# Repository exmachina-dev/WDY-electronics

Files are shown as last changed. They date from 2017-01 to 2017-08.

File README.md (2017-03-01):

```
_ _ _ ___  _   _    ____ _    ____ ____ ___ ____ ____ _  _ _ ____ ____ 
| | | |  \  \_/  __ |___ |    |___ |     |  |__/ |  | |\ | | |    [__  
|_|_| |__/   |      |___ |___ |___ |___  |  |  \ |__| | \| | |___ ___] 
                                                                        
```

# WDY electronics

This repo contains all necessary files to design and produce PCBs for the WDY product range.

## File format and folder structure

Documentation files should be in PDF. Board image files can be in PNG or PDF.

PCB Design file are in EAGLE Standard edition (7.4) file format.

These are general rules to help maintain a consistent folder structure:

* All libraries are placed inside the shared libraries repository. It can be found
  on [Github](https://github.com/exmchina-dev/eagle-resources)

* One board for each project folder.  

* Mutiples revisions can be placed inside a subfolder. i.e. HMI_Board/Rev A1  

* BOMs, partlists, spreadsheet should placed inside a BOMs/ folder.  

* Documentations files are in eagle-resources/doc or in doc/ inside a project folder.

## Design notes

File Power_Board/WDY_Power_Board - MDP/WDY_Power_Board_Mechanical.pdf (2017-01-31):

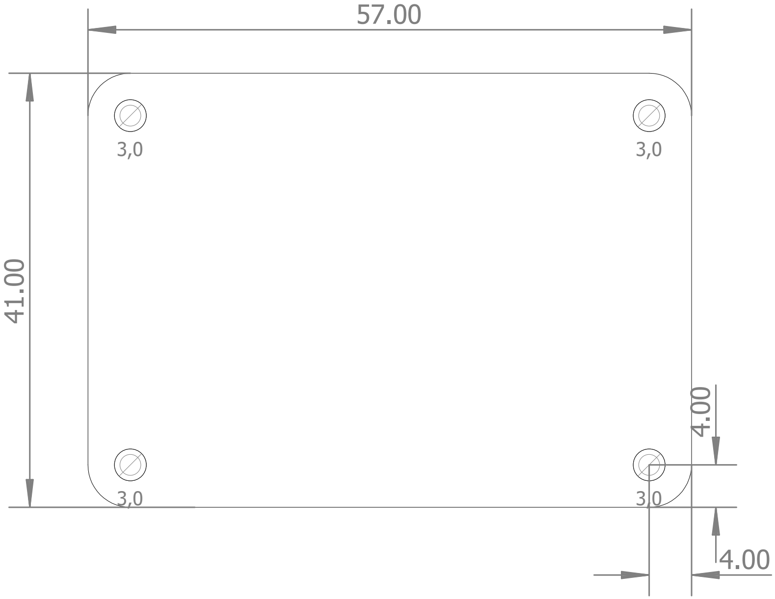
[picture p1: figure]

2017-01-25 11:11 AM f=3.04 C:\Users\Adrian\Documents\ExMachina\repos\WDY-electronics\Power_Board\WDY_Power_Board.brd

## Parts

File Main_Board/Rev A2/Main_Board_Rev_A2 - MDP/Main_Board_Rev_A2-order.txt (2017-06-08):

Quantity	Value	Package	Order code	Manufacturer	Manuf. Code	Availability	Price (from)	Description
1	4.7uF	CT3216	58R3271		F931A475MAA	1092	0.194	AVX (FORMERLY KNOWN AS NICHICON) - F931A475MAA - TANTALUM CAPACITOR, 4.7UF, 10V, 4 OHM, 0.2, 3216-12
10	100nF	C0603	06R4925		MC0603B104K250CT	4139	0.0040	MULTICOMP - MC0603B104K250CT - CERAMIC CAPACITOR, 0.1UF, 25V, X7R, 10%, 0603
3	10uF	CT3216	58R3260		F931A106MAA	1904	0.072	AVX (FORMERLY KNOWN AS NICHICON) - F931A106MAA - TANTALUM CAPACITOR, 10UF, 10V, 3 OHM, 0.2, 3216-12
1	4700pF	C0603	33R0458		MC0603B472K500CT	29799	0.013	MULTICOMP - MC0603B472K500CT - Multilayer Ceramic Capacitor, MC Series, 4700 pF,   10%, X7R, 50 V, 0603 [1608 Metric] 
26	0.1uF	C0603	06R4923		MC0603B104K160CT	46022	0.0040	MULTICOMP - MC0603B104K160CT - CERAMIC CAPACITOR, 0.1UF, 16V, X7R, 10%, 0603
2	18pF	C0603	06R5140		MC0603N180K500CT	3530	0.01	MULTICOMP - MC0603N180K500CT - CERAMIC CAPACITOR 18PF 50V, C0G, 10%, 0603
2	4.7uF	C0603	06X6198		MC0603X475K100CT	71030	0.027	MULTICOMP - MC0603X475K100CT - Multilayer Ceramic Capacitor, MC Series, 4.7  F,   10%, X5R, 10 V, 0603 [1608 Metric] 
4	2.2uF	C0603	01AC8938		GRT188R61H225KE13D	2465	0.113	MURATA - GRT188R61H225KE13D - CAP, MLCC, AEC-Q200, X5R, 2.2UF/50V, 0603
2	1000pF	C0603	06R4910		MC0603B102K500CT	4893	0.0040	MULTICOMP - MC0603B102K500CT - CERAMIC CAPACITOR 1000PF, 50V, X7R, 10%, 0603
2	22uF	C0805	33R0743		MC0805X226M6R3CT	108295	0.097	MULTICOMP - MC0805X226M6R3CT - Multilayer Ceramic Capacitor, MC Series, 22  F,   20%, X5R, 6.3 V, 0805 [2012 Metric] 
2	MBRS140	DO-214AA	83H7272	ON SEMICONDUCTOR	MBRS140T3G	794	0.153	ON SEMICONDUCTOR - MBRS140T3G - SCHOTTKY RECTIFIER, 1A, 40V, 403A
1	1812L110/24DR	LITTLEFUSE_SMD	22M2711		3557	44894	0.11	KEYSTONE - 3557 - FUSE CLIP, 0.8 X 2.8MM, PCB MOUNT
3	22-05-7028-02	7395-02	25M1728		22-05-7028	229	0.475	MOLEX - 22-05-7028 - WIRE-BOARD CONNECTOR HEADER 2 POSITION, 2.54MM
1	RB1-125BAG1A	WIZNET_RB1-125BAG1A	unknown					
1	5504F1-09S-02A-03	5504F1-09S-02A	18T0703		5504F1-09S-02A-03	682	0.836	MULTICOMP - 5504F1-09S-02A-03 - D SUB CONNECTOR, STANDARD, 9 POSITION, RECEPTACLE
4	22-05-7038-03	7395-03	26M6362		22-05-7038	40	0.52	MOLEX - 22-05-7038 - Wire-To-Board Connector, Right Angle, KK 7395 Series, Through Hole, Header, 3, 2.54 mm 
2	22-05-7058-05	7395-05	55H9619	MOLEX	22-05-7058	161	0.685	MOLEX - 22-05-7058 - WIRE-BOARD CONNECTOR HEADER 5 POSITION, 2.54MM
2	22-05-7048-04	7395-04	26M6363		22-05-7048	7713	0.601	MOLEX - 22-05-7048 - Wire-To-Board Connector, Right Angle, KK 7395 Series, Through Hole, Header, 4, 2.54 mm 
2	90814-0208	MOLEX_90814-0208	34R6216		90814-0208	279	0.667	MOLEX - 90814-0208 - Wire-To-Board Connector, Picoflex 90814 Series, Surface Mount, Header, 8, 1.27 mm 
1	90814-0206	MOLEX_90814-0206	34R6215		90814-0206	253	0.632	MOLEX - 90814-0206 - Wire-To-Board Connector, Picoflex 90814 Series, Surface Mount, Header, 6, 1.27 mm 
1	MSTBA2	MSTBA2	71C4161	FARNELL	1757242	2064	0.556	PHOENIX CONTACT - 1757242 - PIN HEADER, 2 POSITION, 5.08MM
1	22-27-2061-06	6410-06	56H0719	MOLEX	22-27-2061	115	0.276	MOLEX - 22-27-2061 - WIRE-BOARD CONNECTOR HEADER 6 POSITION, 2.54MM
1	USB3075-30-A	USB_MICROB_SMT	58T0863		USB3075-30-A	4042	0.418	GCT (GLOBAL CONNECTOR TECHNOLOGY) - USB3075-30-A - MICRO USB, 2.0 TYPE B, RECEPTACLE, SMT
1	1241050-5	2.54/2X5	98K5467		1241050-5	78	3.55	AMP - TE CONNECTIVITY - 1241050-5 - CONNECTOR, HEADER, 2.54MM, 10 POSITION
4	FIDUCIAL1X2	FIDUCIAL-1X2	unknown					
4	G6K-2G-Y	G6K-2G-Y	17C6944	OMRON COMPONENTS USA	G6K-2G-YDC24 BY OMR	0	3.25	OMRON ELECTRONIC COMPONENTS - G6K-2G-YDC24 BY OMR - SIGNAL RELAY, DPDT, 24VDC, 1A, SMD
1	0603PS-103KLB	0603	unknown					
1	15uH	WE-PD2_5848/5820	08P2818		744774115	0	1.27	WURTH ELEKTRONIK - 744774115 - INDUCTOR, UN-SHIELDED, 15UH, 1.9A, SMD
1	10uH	WE-PD2_5848/5820	08P2817		74477410	150	1.27	WURTH ELEKTRONIK - 74477410 - INDUCTOR, UN-SHIELDED, 10UH, 2.5A, SMD
9	Blue	CHIPLED_0603	15R2205		OVS-0603	115	0.159	MULTICOMP - OVS-0603 - LED, BLUE, 0.8MM X 1MM, 100MCD, 465NM
1	Red	CHIPLED_0603	15R2208		OVS-0608	3693	0.248	MULTICOMP - OVS-0608 - LED, RED, 0.8MM X 1MM, 300MCD, 625NM
4	MOUNT-PAD3,0	P3,0	unknown					
2	220	R0603	86T3577		MCMR06X2200FTL	400	0.0010	MULTICOMP - MCMR06X2200FTL - Surface Mount Thick Film Resistor, MCMR Series, 220 ohm, 0.1 W, -  1%, 75 V, 0603 [1608 Metric] 
4	49.9	R0603	86T3659		MCMR06X49R9FTL	15170	0.033	MULTICOMP - MCMR06X49R9FTL - Surface Mount Chip Resistor, Ceramic, MCMR Series, 49.9 ohm, 100 mW,   1%, 75 V, 0603 [1608 Metric] 
4	60.4	R0603	86T3680		MCMR06X60R4FTL	4840	0.027	MULTICOMP - MCMR06X60R4FTL - Surface Mount Chip Resistor, Ceramic, MCMR Series, 60.4 ohm, 100 mW,   1%, 75 V, 0603 [1608 Metric] 
11	4K7	R0603	86T3649		MCMR06X4701FTL	167711	0.033	MULTICOMP - MCMR06X4701FTL - Surface Mount Chip Resistor, Ceramic, MCMR Series, 4.7 kohm, 100 mW,   1%, 75 V, 0603 [1608 Metric] 
1	2K2	R0603	86T3578		MCMR06X2201FTL	9936	0.033	MULTICOMP - MCMR06X2201FTL - Surface Mount Chip Resistor, Ceramic, MCMR Series, 2.2 kohm, 100 mW,   1%, 75 V, 0603 [1608 Metric] 
9	10K	R0603	86T3506		MCMR06X1002FTL	93720	0.027	MULTICOMP - MCMR06X1002FTL - Surface Mount Thick Film Resistor, MCMR Series, 10 kohm, 0.1 W, -  1%, 75 V, 0603 [1608 Metric] 
4	0R	R0603	86T3500		MCMR06X000 PTL	14210	0.013	MULTICOMP - MCMR06X000 PTL - Surface Mount Chip Resistor, Ceramic, MCMR Series, 0 ohm, 100 mW,   0.05ohm, 75 V, 0603 [1608 Metric] 
10	1K5	R0603	86T3542		MCMR06X1501FTL	18540	0.033	MULTICOMP - MCMR06X1501FTL - Surface Mount Chip Resistor, Ceramic, MCMR Series, 1.5 kohm, 100 mW,   1%, 75 V, 0603 [1608 Metric] 
14	100	R0603	86T3504		MCMR06X1000FTL	65873	0.033	MULTICOMP - MCMR06X1000FTL - Surface Mount Chip Resistor, Ceramic, MCMR Series, 100 ohm, 100 mW,   1%, 75 V, 0603 [1608 Metric] 
2	374K	R0603	27W4235		CRCW0603374KFKEA.	3806	0.026	VISHAY - CRCW0603374KFKEA. - Surface Mount Thick Film Resistor, AEC-Q200 CRCW Series, 374 kohm, 100 mW, -  1%, 75 V 
11	1K	R0603	86T3505		MCMR06X1001FTL	60908	0.033	MULTICOMP - MCMR06X1001FTL - Surface Mount Thick Film Resistor, MCMR Series, 1 kohm, 0.1 W, -  1%, 75 V, 0603 [1608 Metric] 
3	2K7	R0603	86T3598		MCMR06X2701FTL	5441	0.033	MULTICOMP - MCMR06X2701FTL - Surface Mount Chip Resistor, Ceramic, MCMR Series, 2.7 kohm, 100 mW,   1%, 75 V, 0603 [1608 Metric] 
3	31K6	R0603	79M5962		MC0603SAF3162T5E	1508	0.0020	MULTICOMP - MC0603SAF3162T5E - RES, THICK FILM, 31K6, 1%, 0.1W, 0603
1	52K3	R0603	26M0962		MC0063W0603152K3	0		MULTICOMP - MC0063W0603152K3 - SMD Current Sense Resistors, MC Series, 52.3 kohm, 63 mW, -  1%, 50 V, 0603 [1608 Metric] 
2	33	R0603	86T3614		MCMR06X33R0FTL	0	0.033	MULTICOMP - MCMR06X33R0FTL - Surface Mount Thick Film Resistor, MCMR Series, 33 ohm, 100 mW, -  1%, 75 V, 0603 [1608 Metric] 
2	B3FS-1050	B3FS	18J2451	FARNELL	B3FS-1050	4815	2.02	OMRON ELECTRONIC COMPONENTS - B3FS-1050 - SWITCH, SPNO, EXTENDED
1	EXMACHINA-LOGO-NAME	EXM-LOGO-BASELINE	unknown					
1	MMBT2222AL	SOT-23	10N9478		MMBT2222ALT3G	13673	0.017	ON SEMICONDUCTOR - MMBT2222ALT3G - BIPOLAR TRANSISTOR, NPN, 40V SOT-23
6	TPB1,27	B1,27	unknown					
1	DP83848JSQ/NOPB	SQA40B	96W2841		DP83848JSQ/NOPB	695	1.3	TEXAS INSTRUMENTS - DP83848JSQ/NOPB - Ethernet Controller, 100 Mbps, IEEE 802.3, IEEE 802.3u, 3 V, 3.6 V, WQFN, 40 
1	MCP2561-E/SN	SOIC127P600X175-8N	12X8698		MCP2561-E/SN	901	0.984	MICROCHIP - MCP2561-E/SN - CAN Bus, Transceiver, CAN, LIN, 1, 1, 4.5 V, 5.5 V, SOIC 
1	AT24C512C-SSHM-B	SOIC127P600X175-8N	68T4128		AT24C512C-SSHM-B	181	1.39	MICROCHIP - AT24C512C-SSHM-B - SERIAL EEPROM, 512KBIT, 1MHZ, SOIC-8
1	LPC1768FBD100	SOT407-1	15R1840		LPC1768FBD100	4173	7.65	NXP - LPC1768FBD100 - 32 BIT MICROCONTROLLER MCU ARM CORTEX 100MHZ LQFP-100
1	TLV313	SOT23-DBV	95Y0395		TLV313IDBVT	1311	0.547	TEXAS INSTRUMENTS - TLV313IDBVT - OP-AMP, 1MHZ, 0.5V/US, SOT-23-5
2	SN74LVC2G17DBVR	SOT95P280X145-6N	76C4207	TEXAS INSTRUMENTS	SN74LVC2G17DBVR	2837	0.201	TEXAS INSTRUMENTS - SN74LVC2G17DBVR - SCHMITT TRIGGER BUFFER, 2BIT, SOT-23-6
3	SN74LVC3G17DCTR	SOP65P400X130-8N	90H3713	TEXAS INSTRUMENTS	SN74LVC3G17DCTR	2807	0.324	TEXAS INSTRUMENTS - SN74LVC3G17DCTR - SCHMITT TRIGGER BUFFER, SSOP-8
1	TPL0401A	SC-70-DCK	82Y6761		ISL90727WIE627Z-T7A	0	1.28	INTERSIL - ISL90727WIE627Z-T7A - DIGITAL POT, 10K, 128, SINGLE, SC-70-6
2	LT3686HDDPBF	DFN300X300X80-11N	78R8986		LT3686HDD#PBF	0	5.16	LINEAR TECHNOLOGY - LT3686HDD#PBF - PWM STEP-DOWN DC/DC CONVERTER, DFN10
1	ASE_50	ASE	84R2105		ASE-50.000MHZ-LC-T	1263	1.6	ABRACON - ASE-50.000MHZ-LC-T - OSCILLATOR, 50MHZ, 3.2 X 2.5MM, CMOS
1	FC-135	FC-135	31M4970		Q13FC13500004	291	0.762	EPSON - Q13FC13500004 - CRYSTAL, 32.768KHZ, 12.5PF, 3.2 X 1.5MM
1	ASE-12	ASE	40Y2118		ASE-12.000MHZ-LC-T	746	2.22	ABRACON - ASE-12.000MHZ-LC-T - OSC, 12MHZ, 3.2 X 2.5MM, LVCMOS
1	3000	3000	66F5622	KEYSTONE ELECTR	3000	13295	0.196	KEYSTONE - 3000 - RETAINER CONTACT, 12MM COIN CELL, SMD

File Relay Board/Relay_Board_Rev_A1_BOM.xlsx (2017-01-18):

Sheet: PdG
Project | WDY - Main Board
Board Name | Relay
Document | Bill of Materials
Author | AB
Date | 2017-01-18
Rev | A1

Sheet: BOM
Quantity | Value | Package | Order code | Manufacturer | Manuf. Code | Availability | Price (from) | Description
4 | 22-05-7028-02 | 2007041 | 25M1728 | Molex | 22-05-7028 | 201 | 0.475 | MOLEX - 22-05-7028 - WIRE-BOARD CONNECTOR HEADER 2 POSITION, 2.54MM
2 | 22-05-7038-03 | 2007069 | 26M6362 | Molex | 22-05-7038 | 40 | 0.133 | MOLEX - 22-05-7038 - Wire-To-Board Connector, Right Angle, KK 7395 Series, Through Hole, Header, 3, 2.54 mm
1 | 22-05-7048-04 | 2007100 | 26M6363 | Molex | 22-05-7048 | 1016 | 0.601 | MOLEX - 22-05-7048 - Wire-To-Board Connector, Right Angle, KK 7395 Series, Through Hole, Header, 4, 2.54 mm
6 | 0.1uF | C0603 | 06R4925 | MULTICOMP | MC0603B104K250CT | 4249 | 0.004 | MULTICOMP - MC0603B104K250CT - CERAMIC CAPACITOR, 0.1UF, 25V, X7R, 10%, 0603
4 | Blue | CHIPLED_0603 | 15R2205 | MULTICOMP | OVS-0603 | 0 | 0.188 | MULTICOMP - OVS-0603 - LED, BLUE, 0.8MM X 1MM, 100MCD, 465NM
4 | G6K-2G-Y | G6K-2G-Y | 82T9378 | OMRON Electronic | G6K-2G-Y 24DC | 338 | 3.83 | OMRON ELECTRONIC COMPONENTS - G6K-2G-Y 24DC - Signal Relay, G6K Series, Non Latching, DPDT, SMD, 1 A, 24 VDC
1 | MSTBA2 | MSTBA2 | 71C4161 | FARNELL | 1757242 | 828 | 0.667 | PHOENIX CONTACT - 1757242 - PIN HEADER, 2 POSITION, 5.08MM
8 | 100 | R0603 | 86T3504 | MULTICOMP | MCMR06X1000FTL | 92331 | 0.024 | MULTICOMP - MCMR06X1000FTL - Surface Mount Chip Resistor, Ceramic, MCMR Series, 100 ohm, 100 mW, 1%, 75 V, 0603 [1608 Metric]
4 | 4K7 | R0603 | 86T3649 | MULTICOMP | MCMR06X4701FTL | 202440 | 0.024 | MULTICOMP - MCMR06X4701FTL - Surface Mount Chip Resistor, Ceramic, MCMR Series, 4.7 kohm, 100 mW, 1%, 75 V, 0603 [1608 Metric]
4 | 1K5 | R0603 | 86T3542 | MULTICOMP | MCMR06X1501FTL | 8236 | 0.024 | MULTICOMP - MCMR06X1501FTL - Surface Mount Chip Resistor, Ceramic, MCMR Series, 1.5 kohm, 100 mW, 1%, 75 V, 0603 [1608 Metric]
4 | STPS3L40UF | SMB | 06X0873 | ST Microelectronics | STPS3L40UF | 6285 | 0.201 | STMICROELECTRONICS - STPS3L40UF - Rectifier Diode, Single, 40 V, 3 A, 500 mV, 75 A, 150 C
2 | SN74LVC2G17DBVR | SOT95P280X145-6N | 76C4207 | TEXAS INSTRUMENTS | SN74LVC2G17DBVR | 2988 | 0.159 | TEXAS INSTRUMENTS - SN74LVC2G17DBVR - SCHMITT TRIGGER BUFFER, 2BIT, SOT-23-6

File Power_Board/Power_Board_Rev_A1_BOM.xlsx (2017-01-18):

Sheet: PdG
Project | WDY - Main Board
Board Name | Main Board
Document | Bill Of Materials
Author | AB
Date | 2017-01-18
Rev | A1

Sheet: BOM
Quantity | Value | Package | Order code | Manufacturer | Manuf. Code | Availability | Price (from) | Description
4 | 2.2uF | C0603 | 01AC8938 | Murata | GRT188R61H225KE13D | 5810 | 0.097 | MURATA - GRT188R61H225KE13D - CAP, MLCC, AECQ200, X5R, 2.2UF/50V, 0603
2 | 1000pF | C0603 | 06R4910 | Multicomp | MC0603B102K500CT | 7447 | 0.004 | MULTICOMP - MC0603B102K500CT - CERAMIC CAPACITOR 1000PF, 50V, X7R, 10%, 0603
2 | 22uF | C0805 | 23T7233 | Multicomp | MC0805X226M6R3CT | 1149 | 0.051 | MULTICOMP - MCMT21N220F250CT - Multilayer Ceramic Capacitor, MLCC Series, 22 uF, 20%, XR, 6.8 V, 0805 [2012 Metric]
1 | STPS3L40UF | SMB | 06X0873 | ST Microelectronics | STPS3L40UF | 6563 | 0.214 | STMICROELECTRONICS - STPS3L40UF - Rectifier Diode, Single, 40 V, 3 A, 500 mV, 75 A, 150 C
2 | MBRS140 | DO-214AA | 83H7272 | ON SEMICONDUCTOR | MBRS140T3G | 684 | 0.166 | ON SEMICONDUCTOR - MBRS140T3G - SCHOTTKY RECTIFIER, 1A, 40V, 403A
1 | FUSE3557L | 3557-LITTLE | 22M2711 | Keystone | 3557 | 22952 | 0.112 | KEYSTONE - 3557 - FUSE CLIP, 0.8 X 2.8MM, PCB MOUNT
2 | 22-05-7028-02 | 2007041 | 25M1728 | Molex | 22-05-7028 | 283 | 0.475 | MOLEX - 22-05-7028 - WIRE-BOARD CONNECTOR HEADER 2 POSITION, 2.54MM
1 | 10uH | WE-PD2_5848/5820 | 08P2817 | Wurth Elektronik | 74477410 | 103 | 1.32 | WURTH ELEKTRONIK - 74477410 - INDUCTOR, UN-SHIELDED, 10UH, 2.5A, SMD
1 | 15uH | WE-PD2_5848/5820 | 08P2818 | Wurth Elektronik | 744774115 | 24 | 1.32 | WURTH ELEKTRONIK - 744774115 - INDUCTOR, UN-SHIELDED, 15UH, 1.9A, SMD
2 | Blue | CHIPLED_0603 | 15R2205 | Multicomp | OVS-0603 | 0 | 0.189 | MULTICOMP - OVS-0603 - LED, BLUE, 0.8MM X 1MM, 100MCD, 465NM
2 | Blue | CHIP-LED0603 | 15R2206 | Multicomp | OVS-0604 | 0 | 0.209 | MULTICOMP - OVS-0604 - LED, GREEN, 0.8MM X 1MM, 300MCD, 520NM
3 | 31k6 | R0603 | 58K4488 | Multicomp | MCMR06X3162FTL | 20297 | 0.012 | MULTICOMP - MC0063W060311K5 - RES, THICK FILM, 1K5, 1%, 0.063W, 0603
2 | 4k7 | R0603 | 86T3649 | Multicomp | MCMR06X4701FTL | 203820 | 0.027 | MULTICOMP - MCMR06X4701FTL - Surface Mount Chip Resistor, Ceramic, MCMR Series, 4.7 kohm, 100 mW, 1%, 75 V, 0603 [1608 Metric]
1 | 52k3 | R0603 | 26M0962 | Multicomp | MC0063W0603152K3 | 4499 | 0.024 | MULTICOMP - MC0063W0603152K3 - SMD Current Sense Resistors, MC Series, 52.3 kohm, 63 mW, - 1%, 50 V, 0603 [1608 Metric]
2 | 10k | R0603 | 86T3506 | Multicomp | MCMR06X1002FTL | 27199 | 0.027 | MULTICOMP - MCMR06X1002FTL - Surface Mount Thick Film Resistor, MCMR Series, 10 kohm, 0.1 W, - 1%, 75 V, 0603 [1608 Metric]
4 | 1k5 | R0603 | 58K4488 | Multicomp | MC0063W060311K5 | 20297 | 0.012 | MULTICOMP - MC0063W060311K5 - RES, THICK FILM, 1K5, 1%, 0.063W, 0603
2 | LT3686HDDPBF | DFN300X300X80-11N | 78R8986 | Linear Technology | LT3686HDD#PBF | 88 | 5.16 | LINEAR TECHNOLOGY - LT3686HDD#PBF - PWM STEP-DOWN DC/DC CONVERTER, DFN10
1 | MSTBA2 | MSTBA2 | 71C4161 | Phoenix Contact | 1757242 | 1130 | 0.667 | PHOENIX CONTACT - 1757242 - PIN HEADER, 2 POSITION, 5.08MM

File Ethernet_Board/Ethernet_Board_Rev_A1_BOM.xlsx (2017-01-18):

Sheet: PdG
Project | WDY - Main Board
Board Name | Ethernet Board
Document | Bill of Materials
Author | AB
Date | 2017-01-18
Rev | A1

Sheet: BOM
Quantity | Value | Package | Order code | Manufacturer | Manuf. Code | Availability | Price (from) | Description
1 | 4.7uF | CT3216 | 58R3271 | AVX | F931A475MAA | 1152 | 0.105 | AVX (FORMERLY KNOWN AS NICHICON) - F931A475MAA - TANTALUM CAPACITOR, 4.7UF, 10V, 4 OHM, 0.2, 3216-12
9 | 100nF | C0603 | 06R4925 | Multicomp | MC0603B104K250CT | 4249 | 0.014 | MULTICOMP - MC0603B104K250CT - CERAMIC CAPACITOR, 0.1UF, 25V, X7R, 10%, 0603
2 | 10uF | CT3216 | 58R3260 | AVX | F931A106MAA | 2581 | 0.063 | AVX (FORMERLY KNOWN AS NICHICON) - F931A106MAA - TANTALUM CAPACITOR, 10UF, 10V, 3 OHM, 0.2, 3216-12
1 | STPS3L40UF | SMB | 06X0873 | ST Microelectronics | STPS3L40UF | 6563 | 0.201 | STMICROELECTRONICS - STPS3L40UF - Rectifier Diode, Single, 40 V, 3 A, 500 mV, 75 A, 150 C
1 | 22-05-7028-02 | 2007041 | 25M1728 | Molex | 22-05-7028 | 283 | 0.475 | MOLEX - 22-05-7028 - WIRE-BOARD CONNECTOR HEADER 2 POSITION, 2.54MM
2 | 22-05-7068-06 | 2007161 | 25M1733 | Molex | 22-05-7068 | 11581 | 1.8 | MOLEX - 22-05-7068 - WIRE-BOARD CONNECTOR HEADER 6 POSITION, 2.54MM
1 | RB1-125BAG1A | WIZNET_RB1-125BAG1A | unknown | WIZnet | RB1-125BAG1A |  | 2.74 | Modular Connectors / Ethernet Connectors RJ-45 w/ Transformer connector/ude
2 | 220 | R0603 | 86T3577 | Multicomp | MCMR06X2200FTL | 400 | 0.024 | MULTICOMP - MCMR06X2200FTL - Surface Mount Thick Film Resistor, MCMR Series, 220 ohm, 0.1 W, - 1%, 75 V, 0603 [1608 Metric]
4 | 49.9 | R0603 | 86T3659 | Multicomp | MCMR06X49R9FTL | 21210 | 0.024 | MULTICOMP - MCMR06X49R9FTL - Surface Mount Chip Resistor, Ceramic, MCMR Series, 49.9 ohm, 100 mW, 1%, 75 V, 0603 [1608 Metric]
1 | 4K7 | R0603 | 86T3649 | Multicomp | MCMR06X4701FTL | 202910 | 0.024 | MULTICOMP - MCMR06X4701FTL - Surface Mount Chip Resistor, Ceramic, MCMR Series, 4.7 kohm, 100 mW, 1%, 75 V, 0603 [1608 Metric]
1 | 2K2 | R0603 | 86T3578 | Multicomp | MCMR06X2201FTL | 32492 | 0.024 | MULTICOMP - MCMR06X2201FTL - Surface Mount Chip Resistor, Ceramic, MCMR Series, 2.2 kohm, 100 mW, 1%, 75 V, 0603 [1608 Metric]
1 | DP83848JSQ/NOPB | SQA40B | 96W2841 | Texas Instrument | DP83848JSQ/NOPB | 492 | 1.32 | TEXAS INSTRUMENTS - DP83848JSQ/NOPB - Ethernet Controller, 100 Mbps, IEEE 802.3, IEEE 802.3u, 3 V, 3.6 V, WQFN, 40
1 | ASE_50 | ASE | 84R2105 | Abracon | ASE-50.000MHZ-LC-T | 3944 | 1.82 | ABRACON - ASE-50.000MHZ-LC-T - OSCILLATOR, 50MHZ, 3.2 X 2.5MM, CMOS

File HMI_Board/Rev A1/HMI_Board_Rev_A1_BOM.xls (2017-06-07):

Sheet: Sheet1
Project | WDY
Board Name | HMI Board
Author | AB
Date | 2017-06-06
Rev | A1

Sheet: BOM_HMI_Board
Qty | Value | Device | Package | Parts | Description | MPN | SKU | DataSheet | MOQ | QTY to order | Farnell
4 | Blue | OVS0603 | SML0603 | LED1, LED2, LED3, LED4 | LED | OVS0603 | 1716770 | http://datasheet.octopart.com/OVS-0603-Multicomp-datasheet-12472386.pdf | 10 | 10 | 0.245
4 | 1k | R-EU_R0603 | R0603 | R1, R2, R3, R4 | RESISTOR, European symbol | MCMR06X1001FTL | 2073348 | http://datasheet.octopart.com/MCMR06X1001FTL-Multicomp-datasheet-15896276.pdf | 10 | 10 | 0.0099
6 | 4k7 | R-EU_R0603 | R0603 | R5, R6, R7, R8, R9, R10 | RESISTOR, European symbol | MCMR06X4701FTL | 2073509 | http://datasheet.octopart.com/MCMR06X4701FTL-Multicomp-datasheet-15896276.pdf | 10 | 10 | 0.0099
1 | 90814-0206 | 90814-0206 | MOLEX_90814-0206 | U2 | CONN HEADER 06 POS 1.27MM SMD TIN | 90814-0206 | 1757024 | http://datasheet.octopart.com/908140206-Molex-datasheet-8333233.pdf | 10 | 10 | 0.68
1 | 90814-0208 | 90814-0208 | MOLEX_90814-0208 | U1 | CONN HEADER 8POS 1.27MM SMD TIN | 90814-0208 | 2426402 | http://datasheet.octopart.com/90814-0208-Molex-datasheet-13780264.pdf | 1 | 1 | 0.567
6 | B3FS-1015 | B3FS-1015 | B3FS | SW1, SW2, SW3, SW4, SW5, SW6 |  | B3FS-1015 | 1960996 | http://datasheet.octopart.com/B3FS1015-Omron-datasheet-10910168.pdf | 1 | 6 | 0.554
 |  |  |  |  |  |  |  |  |  |  | 2.0658
Version: 1.2.3.38126
Octopart Add-In is ready

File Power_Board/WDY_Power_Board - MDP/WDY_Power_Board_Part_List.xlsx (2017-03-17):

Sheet: PdG
Project | WDY - Main Board
Board Name | Power Board
Document | Part List
Author | AB
Date | 2017-02-10
Rev | A1

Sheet: BOM
Qty | Value | Parts | Description | MPN
4 | 2.2uF | C1, C2, C5, C6 | CAPACITOR, European symbol | GRT188R61H225KE13D
2 | 1000pF | C3, C4 | CAPACITOR, European symbol | MC0603B102K500CT
2 | 22uF | C7, C8 | CAPACITOR, European symbol | MCMT21N220F250CT
1 | STPS3L40UF | D1 | STMICROELECTRONICS | STPS3L40UF
2 | MBRS140 | D2, D3 | Redresseur Schottky, 40 V, 1 A, Une, DO-214AA, 2 Broche(s), 600 mV | MBRS140T3G
1 | FUSE3557L | F1 | Fuse | 3557
2 | 22-05-7028-02 | J1, J2 | CONNECTOR | 22-05-7028
1 | 10uH | L1 | SMD Power Inductor | 74477410
1 | 15uH | L2 | SMD Power Inductor | 744774115
2 | Blue | LED1, LED2 | LED | OVS-0603
2 | Blue | LED3, LED4 | LED | OVS-0604
3 | 31k6 | R1, R2, R7 | RESISTOR, European symbol | MCMR06X3162FTL
2 | 4k7 | R3, R4 | RESISTOR, European symbol | MCMR06X4701FTL
1 | 52k3 | R5 | RESISTOR, European symbol | MC0063W0603152K3
2 | 10k | R6, R8 | RESISTOR, European symbol | MCMR06X1002FTL
4 | 1k5 | R9, R10, R11, R12 | RESISTOR, European symbol | MC0063W060311K5
2 | LT3686HDDPBF | U1, U2 | 37V/1.2A Step-DownRegulator in 3mm × 3mm DFN | LT3686HDD#PBF
1 | MSTBA2 | X1 | PHOENIX | 1757242

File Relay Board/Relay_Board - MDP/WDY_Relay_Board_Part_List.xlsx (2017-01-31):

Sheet: PdG
Project | WDY - Main Board
Board Name | Relay Board
Document | Part List
Author | AB
Date | 2017-01-25
Rev | A1

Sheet: BOM
Qty | Value | Device | Package | Parts | Description | MPN
4 | 22-05-7028-02 | 22-05-7028-02 | 2007041 | J3, J4, J6, J7 | CONNECTOR | 22-05-7028
2 | 22-05-7038-03 | 22-05-7038-03 | 2007069 | J1, J2 | CONNECTOR | 22-05-7038
1 | 22-05-7048-04 | 22-05-7048-04 | 2007100 | J5 | CONNECTOR | 22-05-7048
6 | 0.1uF | C-EUC0603 | C0603 | C1, C2, C3, C4, C5, C6 | CAPACITOR, European symbol | MC0603B104K250CT
4 | Blue | LEDCHIPLED_0603 | CHIPLED_0603 | LED1, LED2, LED3, LED4 | LED | OVS-0603
4 | G6K-2G-Y | G6K-2G-Y | G6K-2G-Y | K1, K2, K3, K4 | Low Signal Relay | G6K-2G-Y 24DC
1 | MSTBA2 | MSTBA2 | MSTBA2 | X1 | PHOENIX | 1757242
8 | 100 | R-EU_R0603 | R0603 | R1, R2, R3, R4, R9, R10, R13, R16 | RESISTOR, European symbol | MCMR06X1000FTL
4 | 1K5 | R-EU_R0603 | R0603 | R11, R12, R14, R15 | RESISTOR, European symbol | MCMR06X1501FTL
4 | 4K7 | R-EU_R0603 | R0603 | R5, R6, R7, R8 | RESISTOR, European symbol | MCMR06X4701FTL
4 | STPS3L40UF | STPS3L40UF | SMB | D1, D2, D3, D4 | Zener Diode | STPS3L40UF
2 | SN74LVC2G17DBVR | SN74LVC2G17DBVR | SOT95P280X145-6N | U1, U2 | DUAL SCHMITT-TRIGGER BUFFER | SN74LVC2G17DBVR

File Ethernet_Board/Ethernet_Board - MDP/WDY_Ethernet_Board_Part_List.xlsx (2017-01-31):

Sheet: PdG
Project | WDY - Main Board
Board Name | Etheret Board
Document | Part List
Author | AB
Date | 2017-01-25
Rev | A1

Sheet: BOM
Qty | Value | Device | Package | Parts | Description | MPN
1 | 4.7uF | CPOL-EUCT3216 | CT3216 | C1 | POLARIZED CAPACITOR, European symbol | F931A475MAA
9 | 100nF | C-EUC0603 | C0603 | C2, C3, C5, C6, C7, C9, C10, C11, C12 | CAPACITOR, European symbol | MC0603B104K250CT
2 | 10uF | CPOL-EUCT3216 | CT3216 | C4, C8 | POLARIZED CAPACITOR, European symbol | F931A106MAA
1 | STPS3L40UF | STPS3L40UF | SMB | D1 | Diode Schottky 40V 3A Surface Mount SMBflat | STPS3L40UF
1 | 22-05-7028-02 | 22-05-7028-02 | 2007041 | J1 | CONNECTOR | 22-05-7028
2 | 22-05-7068-06 | 22-05-7068-06 | 2007161 | J2, J3 | CONNECTOR | 22-05-7068
1 | RB1-125BAG1A | RB1-125BAG1A | WIZNET_RB1-125BAG1A | P1 | Accessory RJ-45 With Transformer Connector - UDE | RB1-125BAG1A
2 | 220 | R-EU_R0603 | R0603 | R1, R2 | RESISTOR, European symbol | MCMR06X2200FTL
4 | 49.9 | R-EU_R0603 | R0603 | R3, R4, R5, R6 | RESISTOR, European symbol | MCMR06X49R9FTL
1 | 4K7 | R-EU_R0603 | R0603 | R7 | RESISTOR, European symbol | MCMR06X4701FTL
1 | 2K2 | R-EU_R0603 | R0603 | R8 | RESISTOR, European symbol | MCMR06X2201FTL
1 | DP83848JSQ/NOPB | DP83848JSQ/NOPB | SQA40B | U1 | Ethernet Phyter Single Port | DP83848JSQ/NOPB
1 | ASE_50 | ASE | ASE | X1 | 3.3Vdc CMOS SMD CRYSTAL CLOCK OSCILLATOR | ASE-50.000MHZ-LC-T

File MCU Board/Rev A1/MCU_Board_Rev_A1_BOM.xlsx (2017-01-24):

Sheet: PdG
Project | WDY - Main Board
Board Name | MCU Board
Document | Bill Of Materials
Author | AB
Date | 2017-01-24
Rev | A1

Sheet: BOM
Quantity | Value | Package | Order code | Manufacturer | Manuf. Code | Description
1 | 10uF | CT3216 | 58R3260 | AVX | F931A106MAA | AVX (FORMERLY KNOWN AS NICHICON) - F931A106MAA - TANTALUM CAPACITOR, 10UF, 10V, 3 OHM, 0.2, 3216-12
18 | 0.1uF | C0603 | 06R4923 | MULTICOMP | MC0603B104K160CT | MULTICOMP - MC0603B104K160CT - CERAMIC CAPACITOR, 0.1UF, 16V, X7R, 10%, 0603
2 | 18pF | C0603 | 06R5140 | MULTICOMP | MC0603N180K500CT | MULTICOMP - MC0603N180K500CT - CERAMIC CAPACITOR 18PF 50V, C0G, 10%, 0603
3 | 22-05-7068-06 | 2007161 | 25M1733 | MOLEX | 22-05-7068 | MOLEX - 22-05-7068 - WIRE-BOARD CONNECTOR HEADER 6 POSITION, 2.54MM
2 | 22-05-7028-02 | 2007041 | 25M1728 | MOLEX | 22-05-7028 | MOLEX - 22-05-7028 - WIRE-BOARD CONNECTOR HEADER 2 POSITION, 2.54MM
3 | 22-05-7038-03 | 2007069 | 26M6362 | MOLEX | 22-05-7038 | MOLEX - 22-05-7038 - Wire-To-Board Connector, Right Angle, KK 7395 Series, Through Hole, Header, 3, 2.54 mm
4 | 22-05-7048-04 | 2007100 | 26M6363 | MOLEX | 22-05-7048 | MOLEX - 22-05-7048 - Wire-To-Board Connector, Right Angle, KK 7395 Series, Through Hole, Header, 4, 2.54 mm
1 | 22-27-2061-06 | 1647397 | 56H0719 | MOLEX | 22-27-2061 | MOLEX - 22-27-2061 - WIRE-BOARD CONNECTOR HEADER 6 POSITION, 2.54MM
1 | USB3075-30-A | USB_MICROB_SMT | 58T0863 | GLOBAL CONNECTOR TECHNOLOGY | USB3075-30-A | GLOBAL CONNECTOR TECHNOLOGY - USB3075-30-A - MICRO USB, 2.0 TYPE B, RECEPTACLE, SMT
1 | 1241050-5 | 2.54/2X5 | 98K5467 | AMP | 1241050-5 | AMP - TE CONNECTIVITY - 1241050-5 - CONNECTOR, HEADER, 2.54MM, 10 POSITION
1 | 0603PS-103KLB | 603 | 2286330 | CoilCraft | 0603PS-103KLB | COILCRAFT 0603PS-103KLB Surface Mount Power Inductor, 0603PS Series, 10 µH, 380 mA, 210 mA, Shielded, 1.6 ohm
2 | Blue | CHIPLED_0603 | 15R2205 | MULTICOMP | OVS-0603 | MULTICOMP - OVS-0603 - LED, BLUE, 0.8MM X 1MM, 100MCD, 465NM
5 | 4K7 | R0603 | 86T3649 | MULTICOMP | MCMR06X4701FTL | MULTICOMP - MCMR06X4701FTL - Surface Mount Chip Resistor, Ceramic, MCMR Series, 4.7 kohm, 100 mW, 1%, 75 V, 0603 [1608 Metric]
4 | 0R | R0603 | 86T3500 | MULTICOMP | MCMR06X000 PTL | MULTICOMP - MCMR06X000 PTL - Surface Mount Chip Resistor, Ceramic, MCMR Series, 0 ohm, 100 mW, 0.05ohm, 75 V, 0603 [1608 Metric]
2 | 10K | R0603 | 86T3506 | MULTICOMP | MCMR06X1002FTL | MULTICOMP - MCMR06X1002FTL - Surface Mount Thick Film Resistor, MCMR Series, 10 kohm, 0.1 W, - 1%, 75 V, 0603 [1608 Metric]
3 | 1K5 | R0603 | 86T3542 | MULTICOMP | MCMR06X1501FTL | MULTICOMP - MCMR06X1501FTL - Surface Mount Chip Resistor, Ceramic, MCMR Series, 1.5 kohm, 100 mW, 1%, 75 V, 0603 [1608 Metric]
19 | 100 | R0603 | 86T3504 | MULTICOMP | MCMR06X1000FTL | MULTICOMP - MCMR06X1000FTL - Surface Mount Chip Resistor, Ceramic, MCMR Series, 100 ohm, 100 mW, 1%, 75 V, 0603 [1608 Metric]
3 | 33 | R0603 | 86T3614 | MULTICOMP | MCMR06X33R0FTL | MULTICOMP - MCMR06X33R0FTL - Surface Mount Thick Film Resistor, MCMR Series, 33 ohm, 100 mW, - 1%, 75 V, 0603 [1608 Metric]
6 | 1K | R0603 | 86T3505 | MULTICOMP | MCMR06X1001FTL | MULTICOMP - MCMR06X1001FTL - Surface Mount Thick Film Resistor, MCMR Series, 1 kohm, 0.1 W, - 1%, 75 V, 0603 [1608 Metric]
2 | B3FS-1015 | B3FS | 1960996 | OMRON ELECTRONICS | B3FS1015 | OMRON ELECTRONIC COMPONENTS B3FS1015 Tactile Switch, Non Illuminated, 24 V, 50 mA, 1.47 N, Solder
1 | MMBT2222AL | SOT-23 | 84K8795 | ON SEMICONDUCTOR | MMBT2222ALT1G | ON SEMICONDUCTOR - MMBT2222ALT1G - BIPOLAR TRANSISTOR, NPN, 40V,SOT-23
1 | AT24C512C-SSHM-B | SOIC127P600X175-8N | 68T4066 | MICROCHIP | AT24C02C-SSHM-B | MICROCHIP - AT24C02C-SSHM-B - SERIAL EEPROM, 2KBIT, 1MHZ, SOIC-8
1 | LPC1768FBD100 | SOT407-1 | 15R1840 | NXP | LPC1768FBD100 | NXP - LPC1768FBD100 - 32 BIT MICROCONTROLLER MCU ARM CORTEX 100MHZ LQFP-100
1 | TPL0401A | SC-70-DCK | 65T7357 | INTERSIL | ISL90728WIE627Z-TK | INTERSIL - ISL90728WIE627Z-TK - VOLATILE DIGITAL POTENTIOMETER
2 | SN74LVC3G17DCTR | SOP65P400X130-8N | 90H3713 | TEXAS INSTRUMENTS | SN74LVC3G17DCTR | TEXAS INSTRUMENTS - SN74LVC3G17DCTR - SCHMITT TRIGGER BUFFER, SSOP-8
1 | FC-135 | FC-135 | 31M4970 | EPSON | Q13FC13500004 | EPSON - Q13FC13500004 - CRYSTAL, 32.768KHZ, 12.5PF, 3.2 X 1.5MM
1 | ASE-12 | ASE | 40Y2118 | ABRACON | ASE-12.000MHZ-LC-T | ABRACON - ASE-12.000MHZ-LC-T - OSC, 12MHZ, 3.2 X 2.5MM, LVCMOS
1 | 3000 | 3000 | 66F5622 | KEYSTONE ELECTR | 3000 | KEYSTONE - 3000 - RETAINER CONTACT, 12MM COIN CELL, SMD

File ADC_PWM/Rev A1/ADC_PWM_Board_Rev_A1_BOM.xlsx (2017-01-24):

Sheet: PdG
Project | WDY - Main Board
Board Name | ADC/PWM Board
Document | Bill of Materials
Author | AB
Date | 2017-01-24
Rev | A1

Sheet: BOM
Quantity | Value | Package | Order code | Manufacturer | Manuf. Code | Availability | Price (from) | Description | Colonne1 | Colonne2 | Colonne3 | Colonne4 | Colonne5 | Colonne6 | Colonne7 | Colonne8 | Colonne9 | Colonne10
10 | 0.1uF | C0603 | 06R4925 | MULTICOMP | MC0603B104K250CT | 4249 | 0.004 | MULTICOMP - MC0603B104K250CT - CERAMIC CAPACITOR, 0.1UF, 25V, X7R, 10%, 0603
3 | 22-05-7028-02 | 2007041 | 25M1728 | MOLEX | 22-05-7028 | 195 | 0.475 | MOLEX - 22-05-7028 - WIRE-BOARD CONNECTOR HEADER 2 POSITION, 2.54MM
4 | 22-05-7048-04 | 2007100 | 26M6363 | MOLEX | 22-05-7048 | 11995 | 0.601 | MOLEX - 22-05-7048 - Wire-To-Board Connector, Right Angle, KK 7395 Series, Through Hole, Header, 4, 2.54 mm
3 | 22-05-7038-03 | 2007069 | 26M6362 | MOLEX | 22-05-7038 | 40 | 0.133 | MOLEX - 22-05-7038 - Wire-To-Board Connector, Right Angle, KK 7395 Series, Through Hole, Header, 3, 2.54 mm
1 | 22-05-7058-05 | 2007130 | 55H9619 | MOLEX | 22-05-7058 | 196 | 0.685 | MOLEX - 22-05-7058 - WIRE-BOARD CONNECTOR HEADER 5 POSITION, 2.54MM
1 | MSTBA2 | MSTBA2 | 71C4161 | FARNELL | 1757242 | 828 | 0.667 | PHOENIX CONTACT - 1757242 - PIN HEADER, 2 POSITION, 5.08MM
2 | 10K | R0603 | 86T3506 | MULTICOMP | MCMR06X1002FTL | 24613 | 0.024 | MULTICOMP - MCMR06X1002FTL - Surface Mount Thick Film Resistor, MCMR Series, 10 kohm, 0.1 W, - 1%, 75 V, 0603 [1608 Metric]
2 | 1K8 | R0603 | 86T3556 | MULTICOMP | MCMR06X1801FTL | 6621 | 0.024 | MULTICOMP - MCMR06X1801FTL - Surface Mount Chip Resistor, Ceramic, MCMR Series, 1.8 kohm, 100 mW, 1%, 75 V, 0603 [1608 Metric]
6 | 1K | R0603 | 86T3505 | MULTICOMP | MCMR06X1001FTL | 97318 | 0.024 | MULTICOMP - MCMR06X1001FTL - Surface Mount Thick Film Resistor, MCMR Series, 1 kohm, 0.1 W, - 1%, 75 V, 0603 [1608 Metric]
2 | 1K2 | R0603 | 86T3525 | MULTICOMP | MCMR06X1201FTL | 0 | 0.024 | MULTICOMP - MCMR06X1201FTL - Surface Mount Chip Resistor, Ceramic, MCMR Series, 1.2 kohm, 100 mW, 1%, 75 V, 0603 [1608 Metric]
5 | 100 | R0603 | 86T3504 | MULTICOMP | MCMR06X1000FTL | 92251 | 0.024 | MULTICOMP - MCMR06X1000FTL - Surface Mount Chip Resistor, Ceramic, MCMR Series, 100 ohm, 100 mW, 1%, 75 V, 0603 [1608 Metric]
3 | 2K7 | R0603 | 86T3649 | MULTICOMP | MCMR06X4701FTL | 202080 | 0.024 | MULTICOMP - MCMR06X4701FTL - Surface Mount Chip Resistor, Ceramic, MCMR Series, 4.7 kohm, 100 mW, 1%, 75 V, 0603 [1608 Metric]
1 | TLV313 | SOT23-DBV | 95Y0395 | TEXAS INSTRUMENTS | TLV313IDBVT | 1380 | 0.618 | TEXAS INSTRUMENTS - TLV313IDBVT - OP-AMP, 1MHZ, 0.5V/US, SOT-23-5
1 | HCPL0631 | SOIC08 | 52M7944 |  | HCPL-0631-500E | 505 | 3.28 | BROADCOM LIMITED - HCPL-0631-500E - OPTOCOUPLER, TRANSISTOR, 3750VRMS
1 | SN74LVC3G17DCTR | SOP65P400X130-8N | 90H3713 | TEXAS INSTRUMENTS | SN74LVC3G17DCTR | 1536 | 0.255 | TEXAS INSTRUMENTS - SN74LVC3G17DCTR - SCHMITT TRIGGER BUFFER, SSOP-8

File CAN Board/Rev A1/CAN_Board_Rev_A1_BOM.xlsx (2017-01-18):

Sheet: PdG
Project | WDY - Main Board
Board Name | CAN Board
Document | Bill Of Material
Author | AB
Date | 2017-01-18
Rev | A1

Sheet: BOM
Quantity | Value | Package | Order code | Manufacturer | Manuf. Code | Availability | Price (from) | Description
1 | 4700pF | C0603 | 33R0458 | Multicomp | MC0603B472K500CT | 74089 | 0.012 | MULTICOMP - MC0603B472K500CT - Multilayer Ceramic Capacitor, MC Series, 4700 pF, 10%, X7R, 50 V, 0603 [1608 Metric]
1 | 100nF | C0603 | 06R4925 | Multicomp | MC0603B104K250CT | 4249 | 0.014 | MULTICOMP - MC0603B104K250CT - CERAMIC CAPACITOR, 0.1UF, 25V, X7R, 10%, 0603
2 | 22-05-7028-02 | 22-05-7028 | 25M1728 | Molex | 22-05-7028 | 283 | 0.475 | MOLEX - 22-05-7028 - WIRE-BOARD CONNECTOR HEADER 2 POSITION, 2.54MM
1 | 5504F1-09S-02A-03 | 5504F1-09S-02A | 18T0703 | Multicomp | 5504F1-09S-02A-03 | 623 | 0.945 | MULTICOMP - 5504F1-09S-02A-03 - D SUB CONNECTOR, STANDARD, 9 POSITION, RECEPTACLE
2 | 60R4 | R0603 | 86T3680 | Multicomp | MCMR06X60R4FTL | 400 | 0.024 | MULTICOMP - MCMR06X60R4FTL - Surface Mount Chip Resistor, Ceramic, MCMR Series, 60.4 ohm, 100 mW, 1%, 75 V, 0603 [1608 Metric]
1 | MCP2561-E/SN | SOIC127P600X175-8N | 12X8698 | Microchip | MCP2561-E/SN | 1408 | 1.44 | MICROCHIP - MCP2561-E/SN - CAN Bus, Transceiver, CAN, LIN, 1, 1, 4.5 V, 5.5 V, SOIC
1 | MSTBA2 | MSTBA2 | 71C4161 | Phoenix Contact | 1757242 | 828 | 0.667 | PHOENIX CONTACT - 1757242 - PIN HEADER, 2 POSITION, 5.08MM

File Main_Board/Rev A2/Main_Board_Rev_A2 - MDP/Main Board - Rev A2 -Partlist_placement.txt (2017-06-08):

Partlist

Exported from Main_Board_Rev_A2.brd at 2017-06-08 11:09 AM

EAGLE Version 7.7.0 Copyright (c) 1988-2016 CadSoft

Assembly variant: 

Part     Value             Package             Library                        Position (mm)         Orientation

C1       4.7uF             CT3216              rcl                            (11 44)               MR90
C2       100nF             C0603               rcl                            (23.5 38)             R180
C3       100nF             C0603               rcl                            (23.5 50)             R180
C4       10uF              CT3216              rcl                            (36 44.5)             MR90
C5       4700pF            C0603               rcl                            (56 81.5)             R270
C6       100nF             C0603               rcl                            (28.2 39.9)           MR180
C7       100nF             C0603               rcl                            (36 39)               MR180
C8       100nF             C0603               rcl                            (28.2 45.1)           MR180
C9       10uF              CT3216              rcl                            (32 50)               MR270
C10      100nF             C0603               rcl                            (25.8 41.5)           MR0
C11      100nF             C0603               rcl                            (28.5 48)             MR180
C12      100nF             C0603               rcl                            (31 40)               MR90
C13      100nF             C0603               rcl                            (36.8 36.4)           R90
C14      100nF             C0603               rcl                            (48 79.5)             MR270
C15      10uF              CT3216              rcl                            (54.5 61)             MR0
C16      0.1uF             C0603               rcl                            (47.5 48.5)           MR90
C17      0.1uF             C0603               rcl                            (59.6 36)             R90
C18      0.1uF             C0603               rcl                            (49.5 25.6)           MR270
C19      18pF              C0603               rcl                            (48.4 35.7)           R270
C20      0.1uF             C0603               rcl                            (51 55)               MR180
C21      0.1uF             C0603               rcl                            (46.5 53.5)           MR0
C22      0.1uF             C0603               rcl                            (55 56.5)             MR90
C23      0.1uF             C0603               rcl                            (52.3 41)             MR180
C24      18pF              C0603               rcl                            (54.6 35.7)           R270
C25      0.1uF             C0603               rcl                            (58.5 48)             MR180
C26      0.1uF             C0603               rcl                            (58.5 53.5)           MR180
C27      0.1uF             C0603               rcl                            (47.5 13.6)           MR90
C28      0.1uF             C0603               rcl                            (71.5 20)             R180
C29      0.1uF             C0603               rcl                            (71.5 32.5)           R180
C30      0.1uF             C0603               rcl                            (71.5 41)             R180
C31      0.1uF             C0603               rcl                            (71.5 51.5)           R180
C32      0.1uF             C0603               rcl                            (71.2 46.5)           MR180
C33      0.1uF             C0603               rcl                            (71.4 26.4)           MR180
C34      0.1uF             C0603               rcl                            (56.5 14)             MR270
C35      4.7uF             C0603               rcl                            (14 11.5)             R180
C36      4.7uF             C0603               rcl                            (20.9 11.6)           R180
C37      0.1uF             C0603               rcl                            (17.2 70.1)           R0
C38      0.1uF             C0603               rcl                            (17.2 77.1)           R0
C39      0.1uF             C0603               rcl                            (17.2 72.3)           R0
C40      0.1uF             C0603               rcl                            (17.2 79.35)          R0
C41      0.1uF             C0603               rcl                            (17.2 74.85)          R0
C42      0.1uF             C0603               rcl                            (17.2 81.9)           R0
C43      0.1uF             C0603               rcl                            (24 87)               R270
C44      0.1uF             C0603               rcl                            (26.4 79.9)           R90
C45      0.1uF             C0603               rcl                            (20.1 70.2)           MR270
C46      2.2uF             C0603               rcl                            (80 82.5)             R180
C47      2.2uF             C0603               rcl                            (80 63)               R180
C48      1000pF            C0603               rcl                            (86.5 81)             R0
C49      1000pF            C0603               rcl                            (86.5 62)             R0
C50      2.2uF             C0603               rcl                            (78 96)               R180
C51      2.2uF             C0603               rcl                            (78 76)               R180
C52      22uF              C0805               rcl                            (77.6 85)             R0
C53      22uF              C0805               rcl                            (77.6 65.5)           R0
D1       MBRS140           DO-214AA            diode                          (78 92.5)             R0
D2       MBRS140           DO-214AA            diode                          (78 73)               R0
F1       1812L110/24DR     LITTLEFUSE_SMD      fuse2                          (93.5 73)             R270
J1       22-05-7028-02     7395-02             con-molex                      (5 58)                R270
J2       RB1-125BAG1A      WIZNET_RB1-125BAG1A con-wiznet                     (8.5 44)              R270
J3       5504F1-09S-02A-03 5504F1-09S-02A      con-multicomp                  (50 90.5)             R0
J4       22-05-7038-03     7395-03             con-molex                      (95 22.5)             R90
J5       22-05-7038-03     7395-03             con-molex                      (95 33)               R90
J6       22-05-7038-03     7395-03             con-molex                      (95 43.5)             R90
J7       22-05-7038-03     7395-03             con-molex                      (95 54)               R90
J8       22-05-7058-05     7395-05             con-molex                      (44.5 5)              R0
J9       22-05-7048-04     7395-04             con-molex                      (85 5)                R0
J10      22-05-7048-04     7395-04             con-molex                      (72.5 5)              R0
J11      22-05-7058-05     7395-05             con-molex                      (59.008 5)            R0
J12      22-05-7028-02     7395-02             con-molex                      (13.5 5)              R0
J13      22-05-7028-02     7395-02             con-molex                      (20.5 5)              R0
J14      90814-0208        MOLEX_90814-0208    Molex_By_element14_Batch_1     (19.4 93.9)           R0
J15      90814-0208        MOLEX_90814-0208    Molex_By_element14_Batch_1     (6.3 82)              R90
J16      90814-0206        MOLEX_90814-0206    Molex_By_element14_Batch_1     (6.3 67.7)            R90
J17      MSTBA2            MSTBA2              con-phoenix-508                (98 85.5)             R90
J18      22-27-2061-06     6410-06             con-molex                      (18 24)               R270
J19      USB3075-30-A      USB_MICROB_SMT      con-GlobalConnectorTechnology  (32.35 1.5)           R0
J20      1241050-5         2.54/2X5            con-amp                        (7 22)                R90
JP1      FIDUCIAL1X2       FIDUCIAL-1X2        SparkFun                       (3 8.5)               R0
JP2      FIDUCIAL1X2       FIDUCIAL-1X2        SparkFun                       (95.5 8)              R0
JP3      FIDUCIAL1X2       FIDUCIAL-1X2        SparkFun                       (6 92.5)              R0
JP4      FIDUCIAL1X2       FIDUCIAL-1X2        SparkFun                       (91 96)               R0
K1       G6K-2G-Y          G6K-2G-Y            relay                          (84 22.5)             R180
K2       G6K-2G-Y          G6K-2G-Y            relay                          (84 33)               R180
K3       G6K-2G-Y          G6K-2G-Y            relay                          (84 43.5)             R180
K4       G6K-2G-Y          G6K-2G-Y            relay                          (84 53.5)             R180
L1       0603PS-103KLB     0603                coilcraft                      (52.3 43)             MR0
L2       15uH              WE-PD2_5848/5820    Wurth-POWER_MAGNETICS-rev16f   (71.992 87)           R270
L3       10uH              WE-PD2_5848/5820    Wurth-POWER_MAGNETICS-rev16f   (71.992 67)           R270
LED1     Blue              CHIPLED_0603        led                            (46 73.1)             R180
LED2     Blue              CHIPLED_0603        led                            (77.5 20.5)           R180
LED3     Blue              CHIPLED_0603        led                            (77.5 31)             R180
LED4     Blue              CHIPLED_0603        led                            (77.5 41.5)           R180
LED5     Blue              CHIPLED_0603        led                            (77.5 52)             R180
LED6     Red               CHIPLED_0603        led                            (89 74.5)             R0
LED7     Blue              CHIPLED_0603        led                            (88 12)               R180
LED8     Blue              CHIPLED_0603        led                            (80.5 12)             R180
LED9     Blue              CHIPLED_0603        led                            (84.5 12)             R180
LED10    Blue              CHIPLED_0603        led                            (48.35 73.05)         R180
MP1      MOUNT-PAD3,0      P3,0                holes                          (4 96)                R0
MP2      MOUNT-PAD3,0      P3,0                holes                          (96 96)               R0
MP3      MOUNT-PAD3,0      P3,0                holes                          (4 4)                 R0
MP4      MOUNT-PAD3,0      P3,0                holes                          (96 4)                R0
R1       220               R0603               rcl                            (7.7 41.7)            MR180
R2       220               R0603               rcl                            (7.6 46.1)            MR180
R3       49.9              R0603               rcl                            (23.5 40)             R180
R4       49.9              R0603               rcl                            (23.5 43)             R180
R5       49.9              R0603               rcl                            (23.5 45)             R180
R6       49.9              R0603               rcl                            (23.5 48)             R180
R7       60.4              R0603               rcl                            (53.5 84.5)           R270
R8       60.4              R0603               rcl                            (50.5 84.5)           R90
R9       4K7               R0603               rcl                            (27.5 39)             R270
R10      2K2               R0603               rcl                            (38.5 40.6)           MR0
R11      10K               R0603               rcl                            (60.3 28.3)           R90
R12      4K7               R0603               rcl                            (56.2 30.7)           R0
R13      4K7               R0603               rcl                            (52.3 30.7)           R180
R14      0R                R0603               rcl                            (35.4 73.7)           R0
R15      0R                R0603               rcl                            (39 73.7)             R0
R16      10K               R0603               rcl                            (52 37)               MR270
R17      10K               R0603               rcl                            (60 73)               R270
R18      0R                R0603               rcl                            (63 72)               R180
R19      0R                R0603               rcl                            (63 74)               R180
R20      1K5               R0603               rcl                            (46 69.8)             R270
R21      100               R0603               rcl                            (91.1 22.5)           R180
R22      100               R0603               rcl                            (91.1 33)             R180
R23      100               R0603               rcl                            (91.1 43.5)           R180
R24      100               R0603               rcl                            (91.3 54)             R180
R25      60.4              R0603               rcl                            (46.8 9)              R90
R26      60.4              R0603               rcl                            (44.2 8.9)            R90
R27      374K              R0603               rcl                            (48.4 9)              R90
R28      4K7               R0603               rcl                            (75 22)               R0
R29      4K7               R0603               rcl                            (75 30.5)             R0
R30      374K              R0603               rcl                            (42.1 13.6)           R270
R31      4K7               R0603               rcl                            (75 43)               R0
R32      4K7               R0603               rcl                            (75 53.5)             R0
R33      100               R0603               rcl                            (75 20)               R180
R34      100               R0603               rcl                            (75 32.5)             R180
R35      1K5               R0603               rcl                            (77.5 24)             R90
R36      1K5               R0603               rcl                            (77.5 34.5)           R90
R37      100               R0603               rcl                            (75 41)               R180
R38      1K5               R0603               rcl                            (77.5 45)             R90
R39      1K5               R0603               rcl                            (77.5 55.5)           R90
R40      100               R0603               rcl                            (75 51.5)             R180
R41      1K                R0603               rcl                            (86.3 9)              R90
R42      1K                R0603               rcl                            (73.8 9)              R90
R43      2K7               R0603               rcl                            (57.108 9)            R270
R44      2K7               R0603               rcl                            (52.008 9)            R270
R45      2K7               R0603               rcl                            (63.508 9)            R270
R46      1K                R0603               rcl                            (59.008 9)            R90
R47      1K                R0603               rcl                            (53.908 9)            R90
R48      1K                R0603               rcl                            (61.508 9)            R90
R49      10K               R0603               rcl                            (12.2 8.8)            R270
R50      10K               R0603               rcl                            (19.2 8.8)            R90
R51      10K               R0603               rcl                            (14.8 8.8)            R270
R52      10K               R0603               rcl                            (21.8 8.8)            R90
R53      100               R0603               rcl                            (13.5 59)             R0
R54      100               R0603               rcl                            (13.5 64)             R0
R55      100               R0603               rcl                            (13.5 56.4)           R180
R56      100               R0603               rcl                            (13.5 61.5)           R180
R57      4K7               R0603               rcl                            (32 89.8)             R180
R58      4K7               R0603               rcl                            (28.5 89.85)          R0
R59      1K                R0603               rcl                            (13.5 70.1)           R0
R60      1K                R0603               rcl                            (13.5 72.3)           R0
R61      1K                R0603               rcl                            (13.5 74.85)          R0
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

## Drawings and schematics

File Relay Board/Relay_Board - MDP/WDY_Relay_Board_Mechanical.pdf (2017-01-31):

57.00

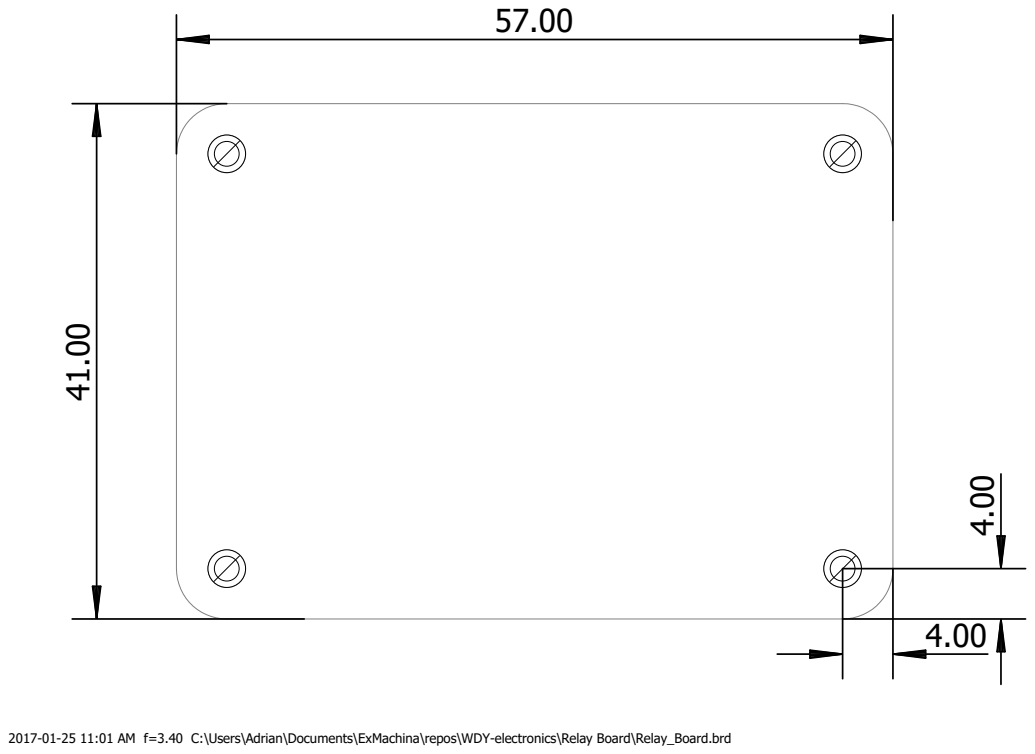
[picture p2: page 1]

2017-01-25 11:01 AM f=3.40 C:\Users\Adrian\Documents\ExMachina\repos\WDY-electronics\Relay Board\Relay_Board.brd 41.00

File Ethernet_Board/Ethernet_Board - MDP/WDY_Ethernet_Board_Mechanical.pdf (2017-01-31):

57.00 41.00

# 4.00 ⁴.00 ³,0

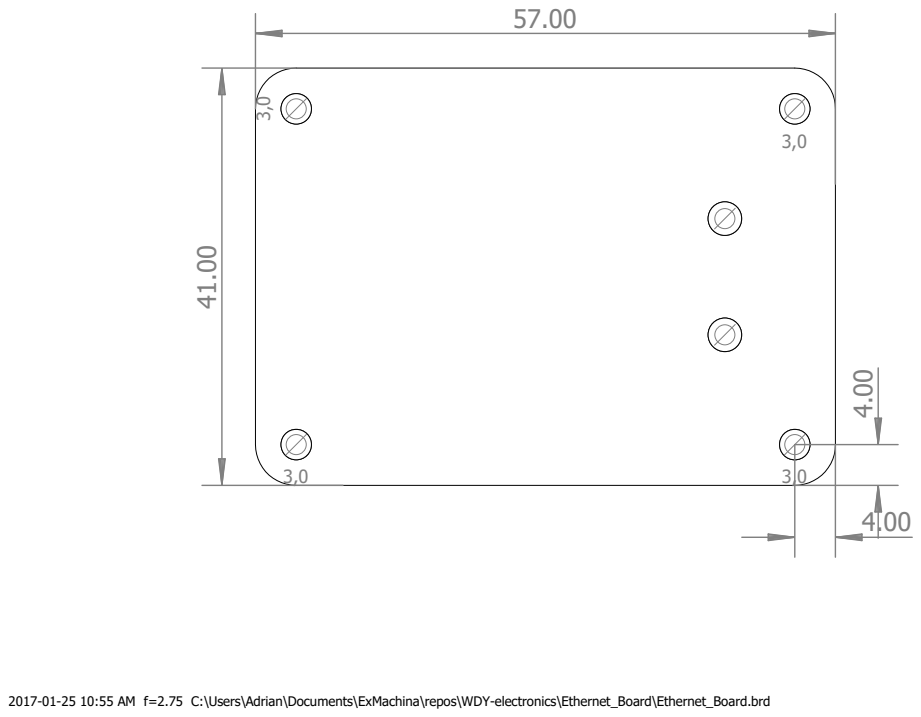
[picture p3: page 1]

2017-01-25 10:55 AM f=2.75 C:\Users\Adrian\Documents\ExMachina\repos\WDY-electronics\Ethernet_Board\Ethernet_Board.brd

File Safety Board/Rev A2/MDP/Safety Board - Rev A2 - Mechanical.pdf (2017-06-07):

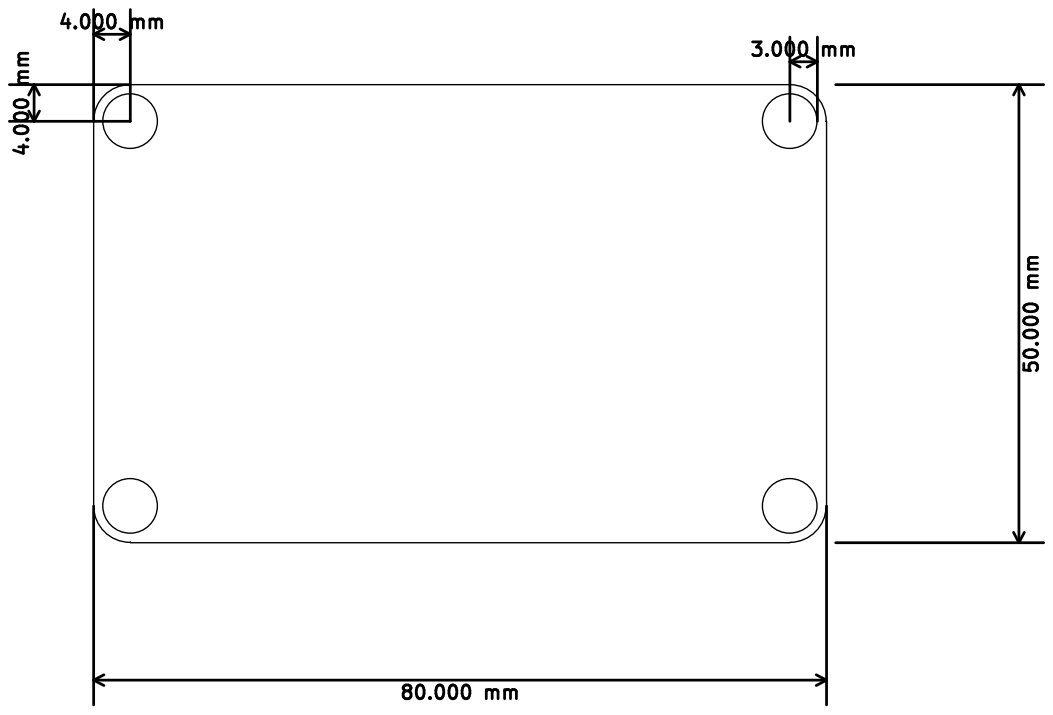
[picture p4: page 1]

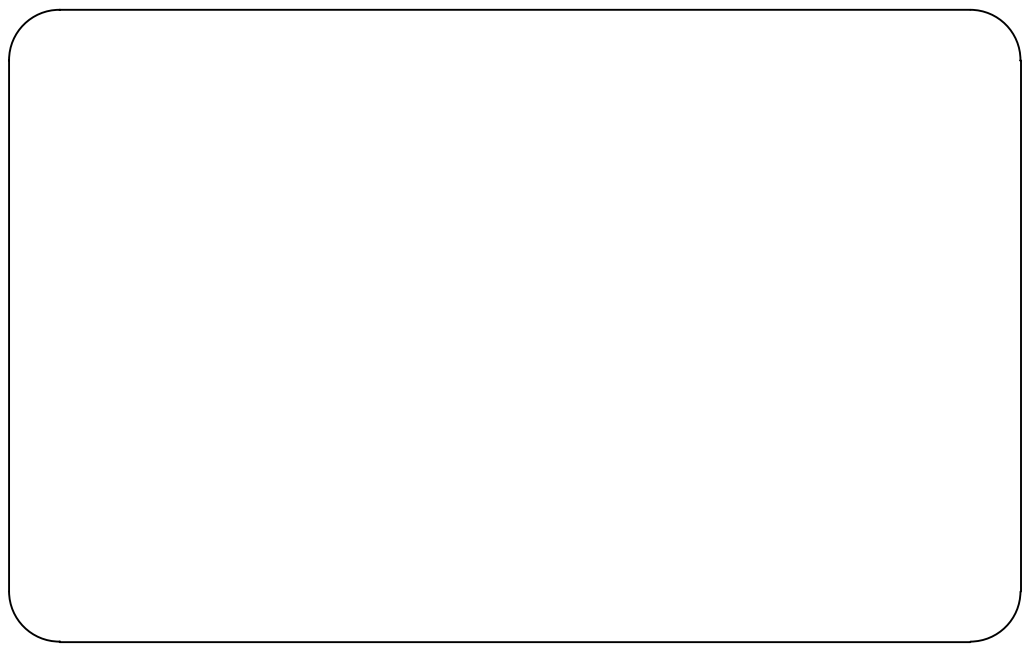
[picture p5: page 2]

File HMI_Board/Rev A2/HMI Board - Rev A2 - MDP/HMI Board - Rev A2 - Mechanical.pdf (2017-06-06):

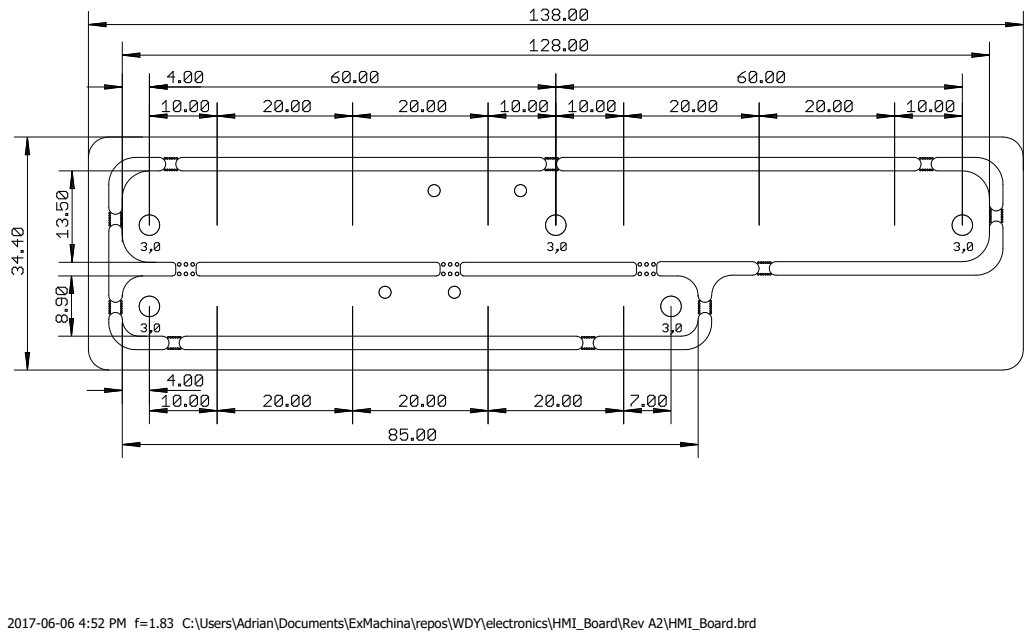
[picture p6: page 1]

2017-06-06 4:52 PM f=1.83 C:\Users\Adrian\Documents\ExMachina\repos\WDY\electronics\HMI_Board\Rev A2\HMI_Board.brd

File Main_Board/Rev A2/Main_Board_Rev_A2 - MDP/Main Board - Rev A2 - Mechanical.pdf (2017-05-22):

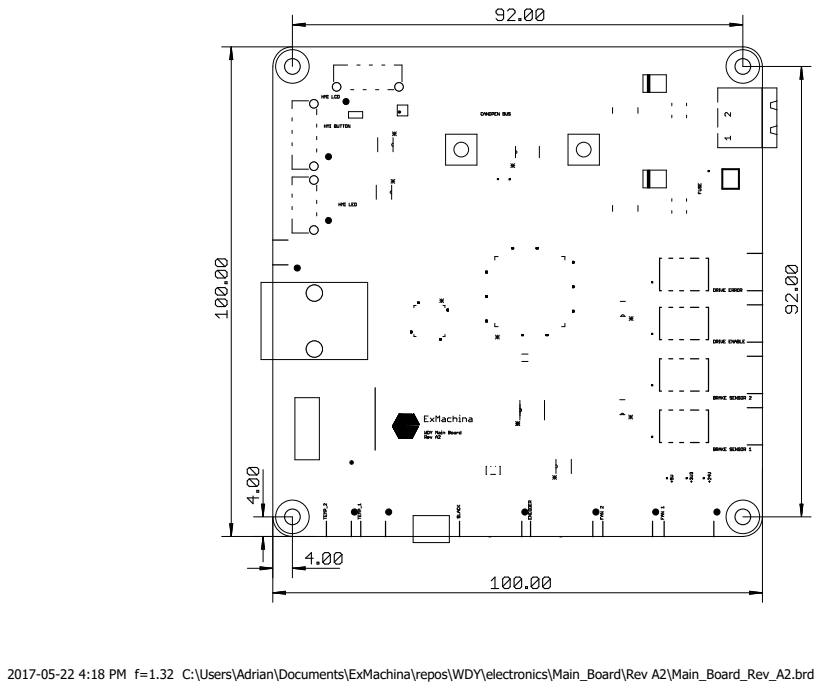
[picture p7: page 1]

2017-05-22 4:18 PM f=1.32 C:\Users\Adrian\Documents\ExMachina\repos\WDY\electronics\Main_Board\Rev A2\Main_Board_Rev_A2.brd

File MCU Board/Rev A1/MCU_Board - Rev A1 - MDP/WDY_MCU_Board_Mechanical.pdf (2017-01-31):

90.00 41.00

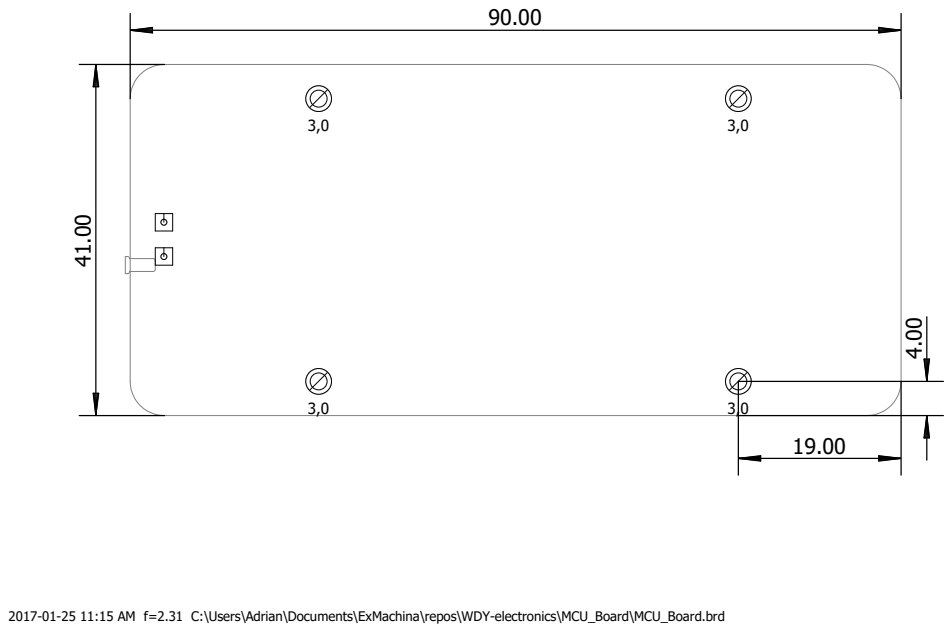
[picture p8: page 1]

2017-01-25 11:15 AM f=2.31 C:\Users\Adrian\Documents\ExMachina\repos\WDY-electronics\MCU_Board\MCU_Board.brd

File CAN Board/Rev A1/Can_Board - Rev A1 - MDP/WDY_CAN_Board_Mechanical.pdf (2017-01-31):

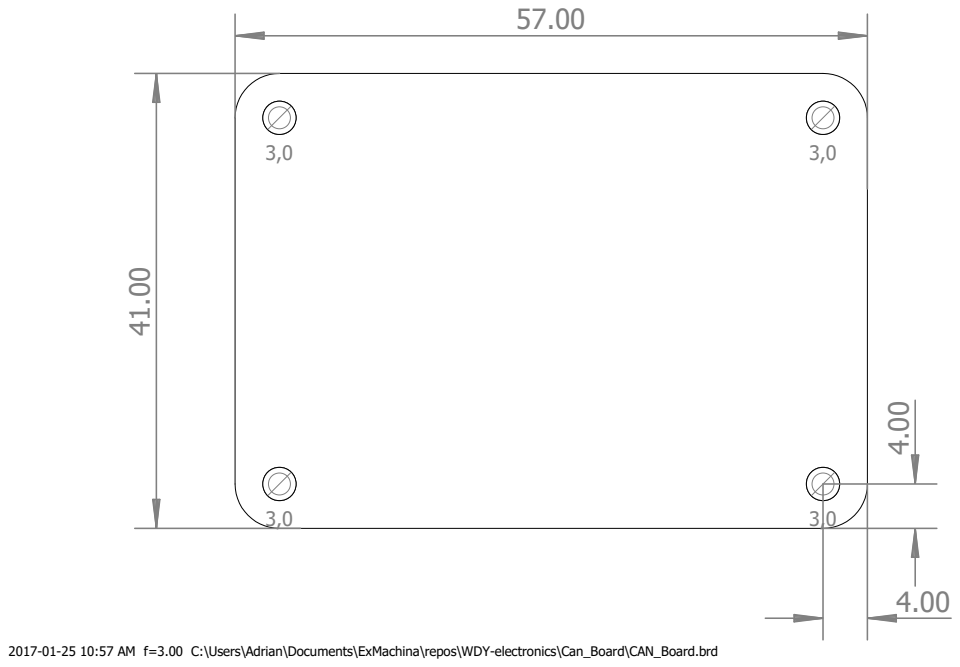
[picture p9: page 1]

2017-01-25 10:57 AM f=3.00 C:\Users\Adrian\Documents\ExMachina\repos\WDY-electronics\Can_Board\CAN_Board.brd

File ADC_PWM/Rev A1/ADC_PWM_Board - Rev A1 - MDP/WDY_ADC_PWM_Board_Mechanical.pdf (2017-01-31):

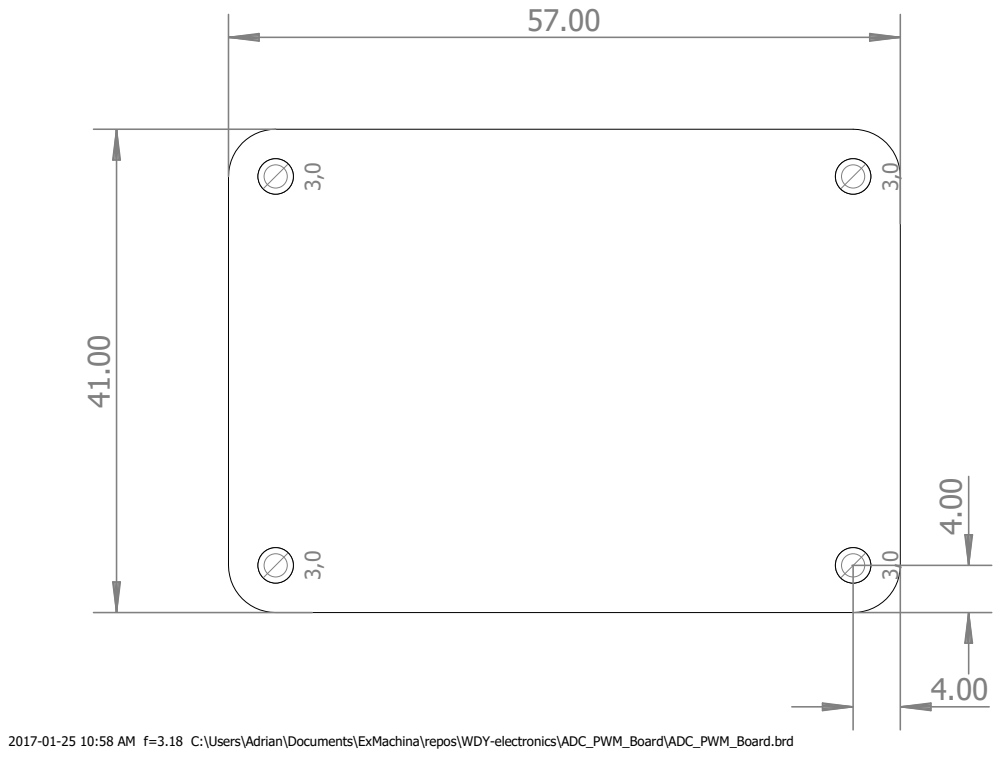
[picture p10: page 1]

2017-01-25 10:58 AM f=3.18 C:\Users\Adrian\Documents\ExMachina\repos\WDY-electronics\ADC_PWM_Board\ADC_PWM_Board.brd

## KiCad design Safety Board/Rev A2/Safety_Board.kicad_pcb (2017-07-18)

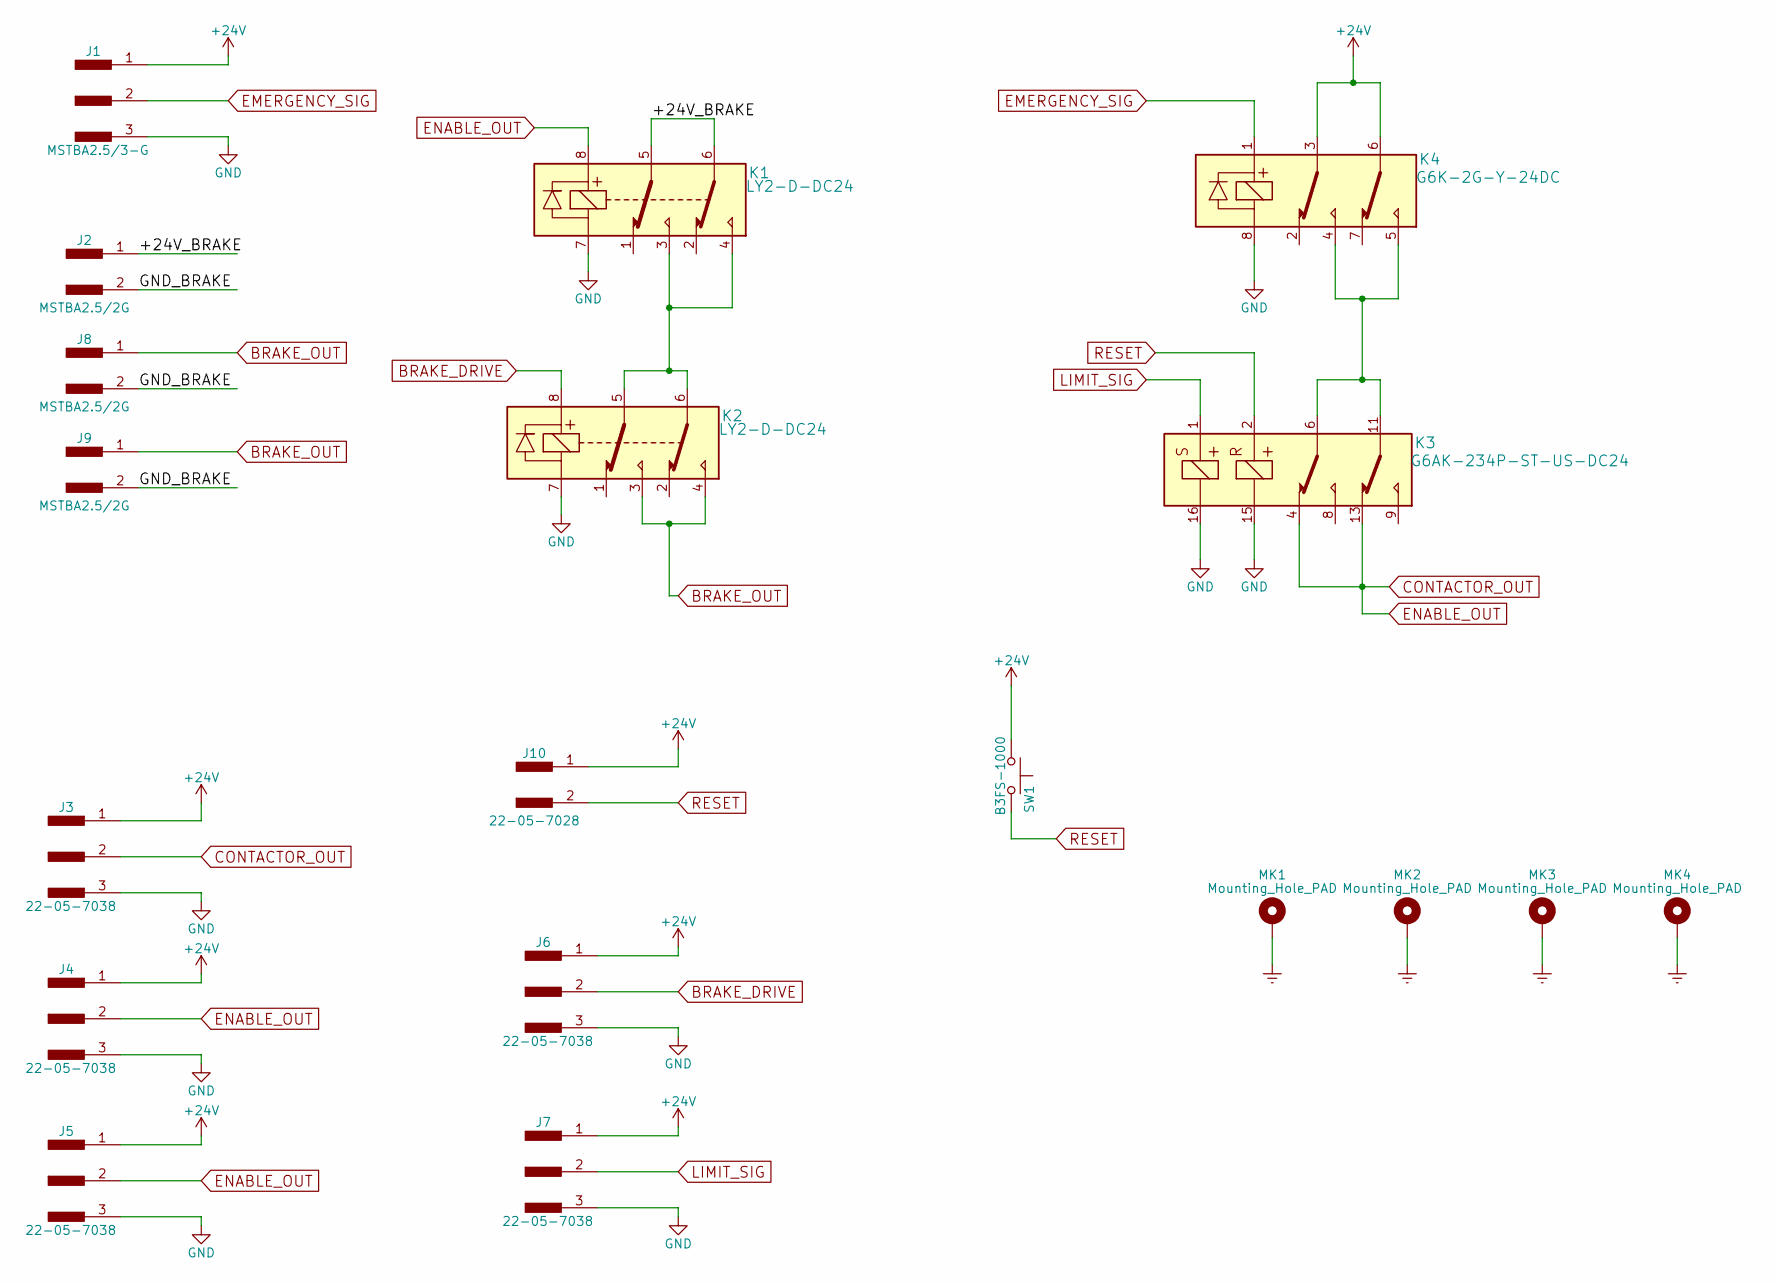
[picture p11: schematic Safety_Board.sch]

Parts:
J1: MSTBA2.5/3-G; MSTBA3
J2, J8, J9: MSTBA2.5/2G; MSTBA2.5
J3, J4, J5, J6, J7: 22-05-7038
J10: 22-05-7028; 7395-02
K1, K2: LY2-D-DC24; PT08-0
K3: G6AK-234P-ST-US-DC24; G6AK-234P-ST-US-DCx
K4: G6K-2G-Y-24DC; G6K-2G-Y
MK1, MK2, MK3, MK4: Mounting_Hole_PAD; MountingHole_3mm_Pad
SW1: B3FS-1000; SW_SPST_B3S-1000

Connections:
+24V: J1.1, J3.1, J4.1, J5.1, J6.1, J7.1, J10.1, K4.3, K4.6, SW1.1
/+24V_BRAKE: J2.1, K1.5, K1.6
/GND_BRAKE: J2.2, J8.2, J9.2
BRAKE_DRIVE: J6.2, K2.8
BRAKE_OUT: J8.1, J9.1, K2.3, K2.4
CONTACTOR_OUT: J3.2, J4.2, J5.2, K1.8, K3.4, K3.13
EMERGENCY_SIG: J1.2, K4.1
Earth: MK1.1, MK2.1, MK3.1, MK4.1
GND: J1.3, J3.3, J4.3, J5.3, J6.3, J7.3, K1.7, K2.7, K3.15, K3.16, K4.8
LIMIT_SIG: J7.2, K3.1
unnamed: K1.3, K1.4, K2.5, K2.6
unnamed: K3.6, K3.11, K4.4, K4.5
RESET: J10.2, K3.2, SW1.2

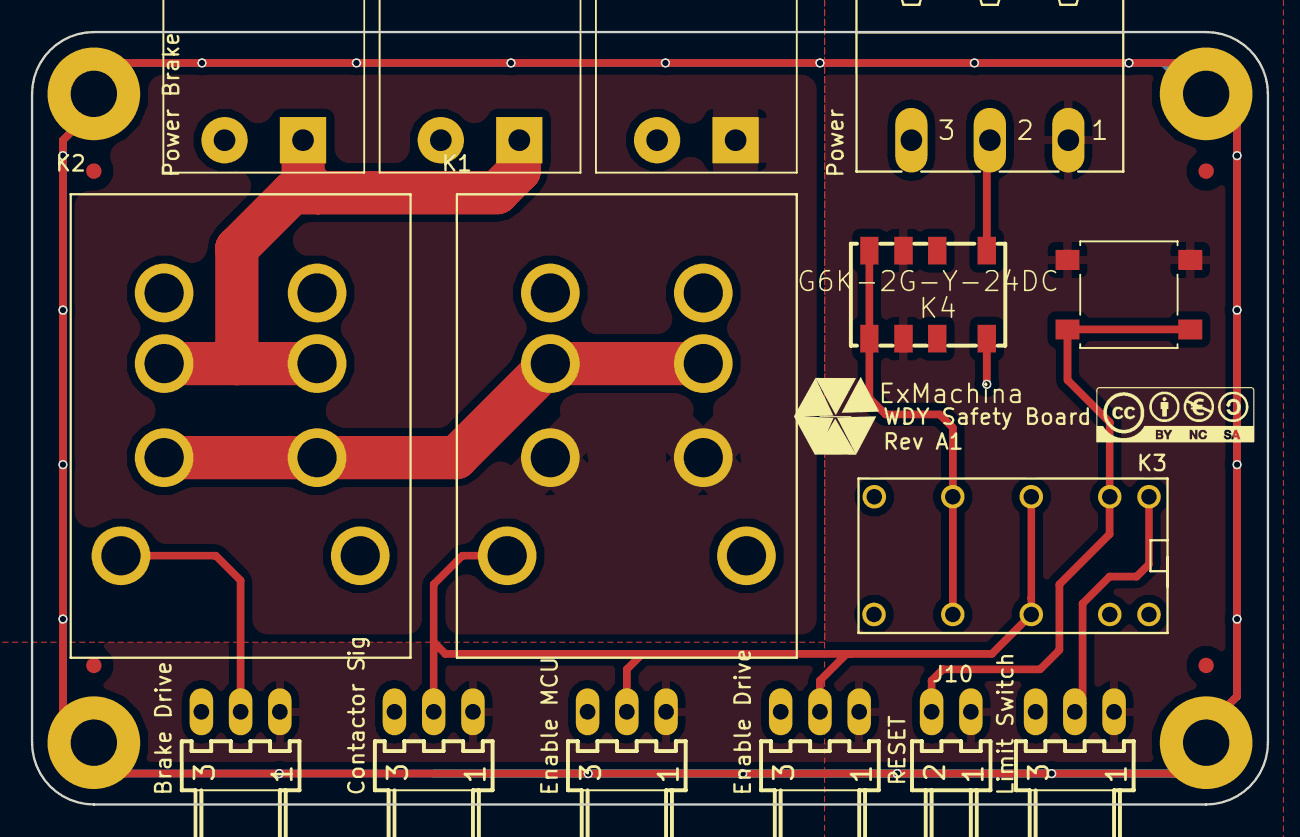
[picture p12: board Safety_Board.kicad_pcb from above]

Board: 2 copper layers, 80.0 x 50.0 mm, 21 parts (0 on the bottom side), 13 nets.

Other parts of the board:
S?: CC-BY-NC-SA
T3: EXMACHINA-LOGO-NAME; EXM-LOGO-BASELINE

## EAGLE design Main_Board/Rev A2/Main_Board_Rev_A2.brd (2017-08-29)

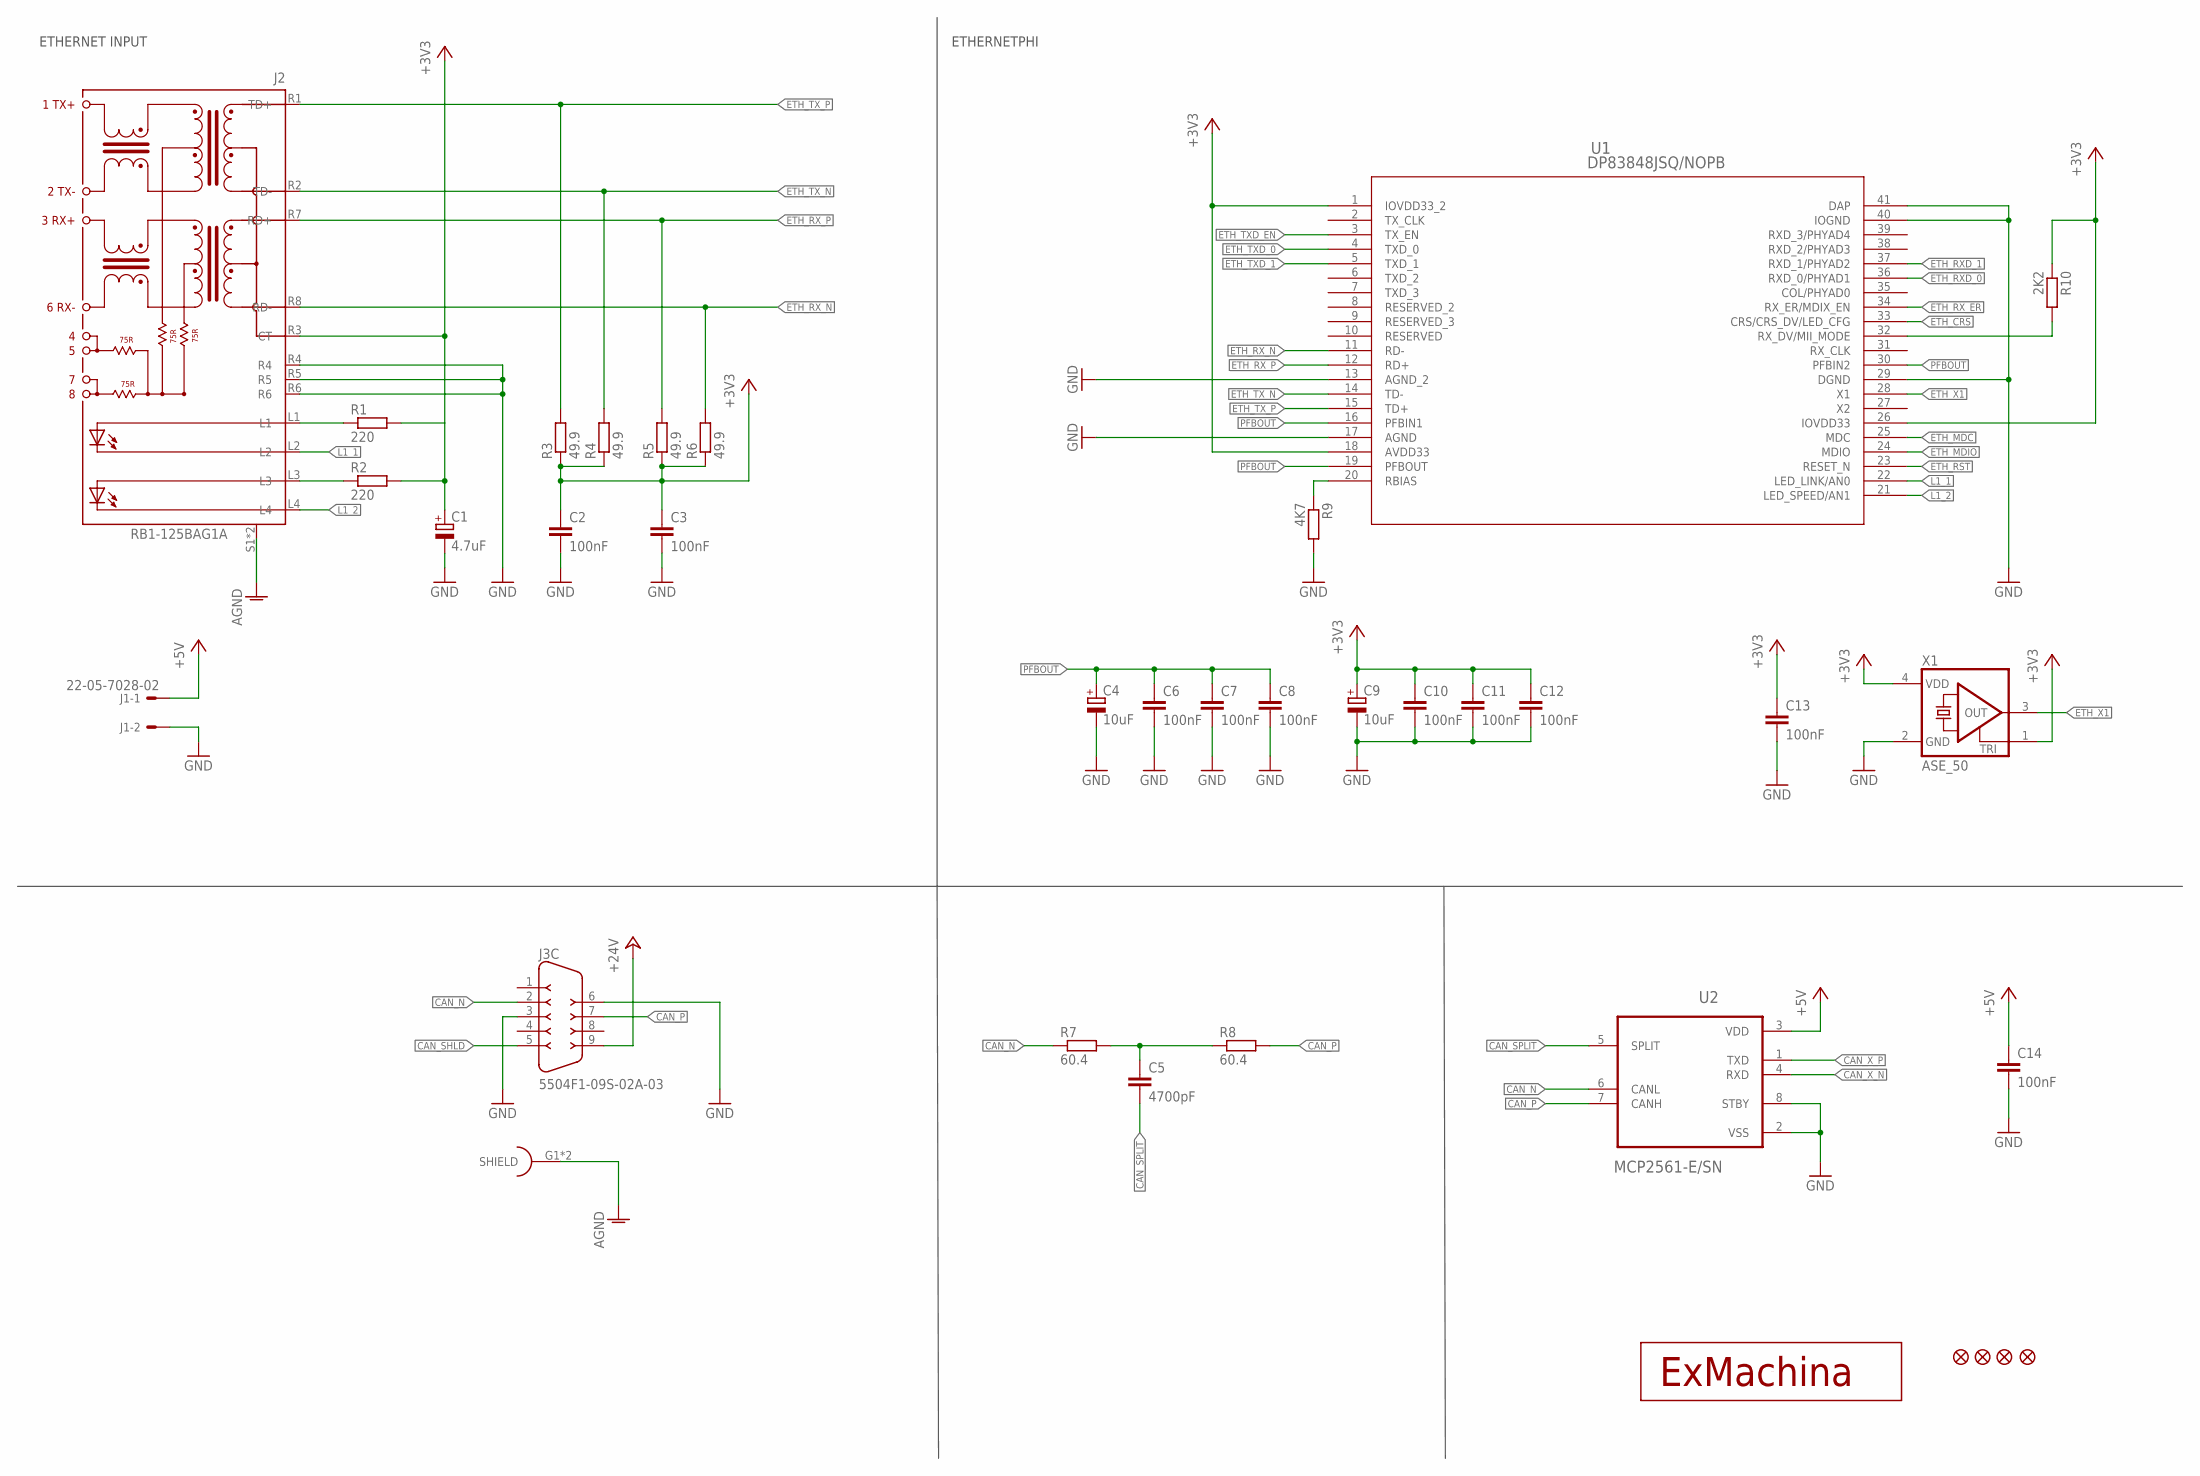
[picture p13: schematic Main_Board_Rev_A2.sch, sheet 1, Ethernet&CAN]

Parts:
C1: 4.7uF; CT3216; MPN F931A475MAA
C2, C3, C6, C7, C8, C10, C11, C12, C13, C14: 100nF; C0603; MPN MC0603B104K250CT
C4, C9: 10uF; CT3216; MPN F931A106MAA
C5: 4700pF; C0603; MPN MC0603B472K500CT
J1: 22-05-7028-02; 7395-02; MPN 22-05-7028
J2: RB1-125BAG1A; WIZNET_RB1-125BAG1A
J3: 5504F1-09S-02A-03; 5504F1-09S-02A; MPN 5504F1-09S-02A-03
JP1, JP2, JP3, JP4: FIDUCIAL1X2; FIDUCIAL-1X2
R1, R2: 220; R0603; MPN MCMR06X2200FTL
R3, R4, R5, R6: 49.9; R0603; MPN MCMR06X49R9FTL
R7, R8: 60.4; R0603; MPN MCMR06X60R4FTL
R9: 4K7; R0603; MPN MCMR06X4701FTL
R10: 2K2; R0603; MPN MCMR06X2201FTL
T1: EXMACHINA-LOGO-NAME; EXM-LOGO-BASELINE
U1: DP83848JSQ/NOPB; SQA40B; MPN DP83848JSQ/NOPB
U2: MCP2561-E/SN; SOIC127P600X175-8N; MPN MCP2561-E/SN
X1: ASE_50; ASE; MPN ASE-50.000MHZ-LC-T

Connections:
+3V3: C1.+, C2.1, C3.1, C9.+, C10.1, C11.1, C12.1, C13.1, J2.R3 (CT), R1.2, R2.2, R3.1, R4.1, R5.1, R6.1, R10.1, U1.1 (IOVDD33_2), U1.18 (AVDD33), U1.26 (IOVDD33), X1.1 (TRI), X1.4 (VDD); also elsewhere on the board
+5V: C14.1, J1.1, U2.3 (VDD); also elsewhere on the board
+24V: J3.9; also elsewhere on the board
AGND: J2.S1, J2.S2, J3.G1 (SHIELD), J3.G2 (SHIELD); also elsewhere on the board
CAN_N: J3.2, R7.1, U2.6 (CANL)
CAN_P: J3.7, R8.2, U2.7 (CANH)
CAN_SHLD: J3.5
CAN_SPLIT: C5.2, U2.5 (SPLIT)
CAN_X_N: U2.4 (RXD); also elsewhere on the board
CAN_X_P: U2.1 (TXD); also elsewhere on the board
ETH_CRS: U1.33 (CRS/CRS_DV/LED_CFG); also elsewhere on the board
ETH_MDC: U1.25 (MDC); also elsewhere on the board
ETH_MDIO: U1.24 (MDIO); also elsewhere on the board
ETH_RST: U1.23 (RESET_N); also elsewhere on the board
ETH_RXD_0: U1.36 (RXD_0/PHYAD1); also elsewhere on the board
ETH_RXD_1: U1.37 (RXD_1/PHYAD2); also elsewhere on the board
ETH_RX_ER: U1.34 (RX_ER/MDIX_EN); also elsewhere on the board
ETH_RX_N: J2.R8 (RD-), R6.2, U1.11 (RD-)
ETH_RX_P: J2.R7 (RD+), R5.2, U1.12 (RD+)
ETH_TXD_0: U1.4 (TXD_0); also elsewhere on the board
ETH_TXD_1: U1.5 (TXD_1); also elsewhere on the board
ETH_TXD_EN: U1.3 (TX_EN); also elsewhere on the board
ETH_TX_N: J2.R2 (TD-), R4.2, U1.14 (TD-)
ETH_TX_P: J2.R1 (TD+), R3.2, U1.15 (TD+)
ETH_X1: U1.28 (X1), X1.3 (OUT); also elsewhere on the board
GND: C1.-, C2.2, C3.2, C4.-, C6.2, C7.2, C8.2, C9.-, C10.2, C11.2, C12.2, C13.2, C14.2, J1.2, J2.R4, J2.R5, J2.R6, J3.3, J3.6, R9.2, U1.13 (AGND_2), U1.17 (AGND), U1.29 (DGND), U1.40 (IOGND), U1.41 (DAP), U2.2 (VSS), U2.8 (STBY), X1.2 (GND); also elsewhere on the board
L1_1: J2.L2, U1.22 (LED_LINK/AN0)
L1_2: J2.L4, U1.21 (LED_SPEED/AN1)
MII_MODE: R10.2, U1.32 (RX_DV/MII_MODE)
unnamed: C5.1, R7.2, R8.1
unnamed: R9.1, U1.20 (RBIAS)
unnamed: J2.L1, R1.1
unnamed: J2.L3, R2.1
PFBOUT: C4.+, C6.1, C7.1, C8.1, U1.16 (PFBIN1), U1.19 (PFBOUT), U1.30 (PFBIN2)

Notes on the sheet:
ETHERNET INPUT
ETHERNETPHI

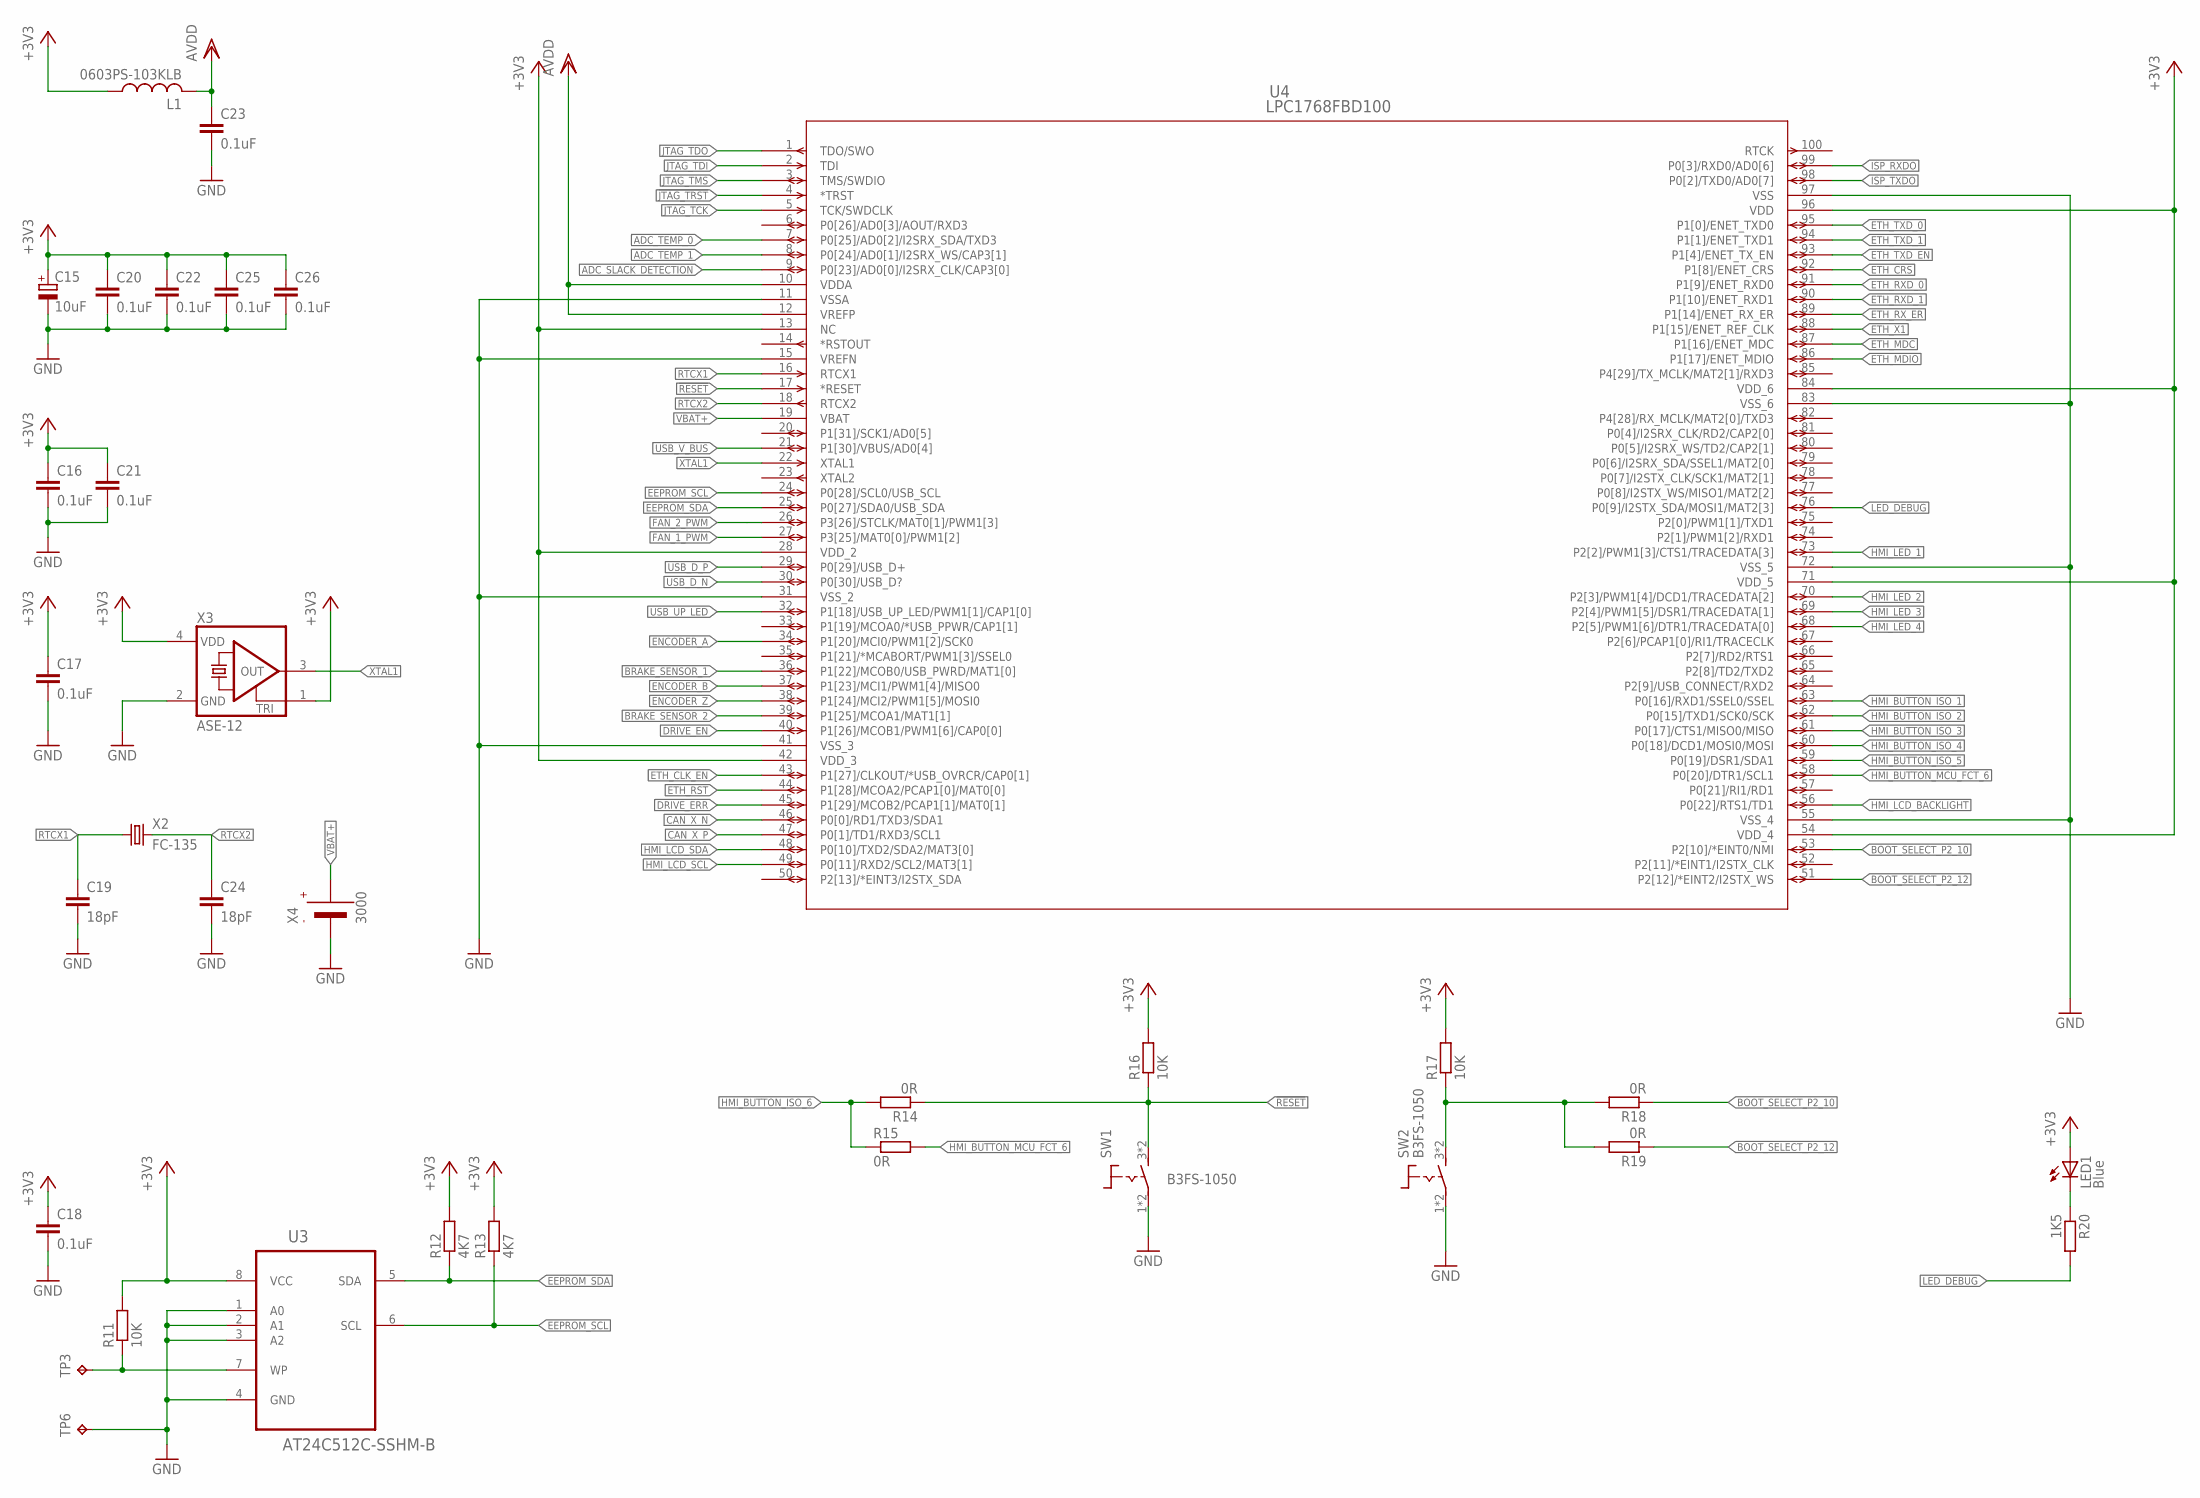
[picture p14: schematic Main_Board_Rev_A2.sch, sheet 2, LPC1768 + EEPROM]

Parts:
C15: 10uF; CT3216; MPN F931A106MAA
C16, C17, C18, C20, C21, C22, C23, C25, C26: 0.1uF; C0603; MPN MC0603B104K160CT
C19, C24: 18pF; C0603; MPN MC0603N180K500CT
L1: 0603PS-103KLB; 0603
LED1: Blue; CHIPLED_0603; MPN OVS-0603
R11, R16, R17: 10K; R0603; MPN MCMR06X1002FTL
R12, R13: 4K7; R0603; MPN MCMR06X4701FTL
R14, R15, R18, R19: 0R; R0603; MPN MCMR06X000 PTL
R20: 1K5; R0603; MPN MCMR06X1501FTL
SW1, SW2: B3FS-1050; B3FS; MPN B3FS-1050
TP3, TP6: TPB1,27; B1,27
U3: AT24C512C-SSHM-B; SOIC127P600X175-8N; MPN AT24C512C-SSHM-B
U4: LPC1768FBD100; SOT407-1; MPN LPC1768FBD100
X2: FC-135; MPN Q13FC13500004
X3: ASE-12; ASE; MPN ASE-12.000MHZ-LC-T
X4: 3000; MPN 3000

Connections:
!JTAG_TRST: U4.4 (*TRST); also elsewhere on the board
!RESET: R14.1, R16.1, SW1.3 (1), SW1.4 (1), U4.17 (*RESET)
+3V3: C15.+, C16.1, C17.1, C18.1, C20.1, C21.1, C22.1, C25.1, C26.1, L1.P$1 (1), LED1.A, R11.2, R12.2, R13.2, R16.2, R17.2, U3.8 (VCC), U4.13 (NC), U4.28 (VDD_2), U4.42 (VDD_3), U4.54 (VDD_4), U4.71 (VDD_5), U4.84 (VDD_6), U4.96 (VDD), X3.1 (TRI), X3.4 (VDD); also elsewhere on the board
ADC_SLACK_DETECTION: U4.9 (P0[23]/AD0[0]/I2SRX_CLK/CAP3[0]); also elsewhere on the board
ADC_TEMP_0: U4.7 (P0[25]/AD0[2]/I2SRX_SDA/TXD3); also elsewhere on the board
ADC_TEMP_1: U4.8 (P0[24]/AD0[1]/I2SRX_WS/CAP3[1]); also elsewhere on the board
AVDD: C23.1, L1.P$2 (2), U4.10 (VDDA), U4.12 (VREFP); also elsewhere on the board
BOOT_SELECT_P2_10: R18.1, U4.53 (P2[10]/*EINT0/NMI)
BOOT_SELECT_P2_12: R19.1, U4.51 (P2[12]/*EINT2/I2STX_WS)
BRAKE_SENSOR_1: U4.36 (P1[22]/MCOB0/USB_PWRD/MAT1[0]); also elsewhere on the board
BRAKE_SENSOR_2: U4.39 (P1[25]/MCOA1/MAT1[1]); also elsewhere on the board
CAN_X_N: U4.46 (P0[0]/RD1/TXD3/SDA1); also elsewhere on the board
CAN_X_P: U4.47 (P0[1]/TD1/RXD3/SCL1); also elsewhere on the board
DRIVE_EN: U4.40 (P1[26]/MCOB1/PWM1[6]/CAP0[0]); also elsewhere on the board
DRIVE_ERR: U4.45 (P1[29]/MCOB2/PCAP1[1]/MAT0[1]); also elsewhere on the board
EEPROM_SCL: R13.1, U3.6 (SCL), U4.24 (P0[28]/SCL0/USB_SCL)
EEPROM_SDA: R12.1, U3.5 (SDA), U4.25 (P0[27]/SDA0/USB_SDA)
ENCODER_A: U4.34 (P1[20]/MCI0/PWM1[2]/SCK0); also elsewhere on the board
ENCODER_B: U4.37 (P1[23]/MCI1/PWM1[4]/MISO0); also elsewhere on the board
ENCODER_Z: U4.38 (P1[24]/MCI2/PWM1[5]/MOSI0); also elsewhere on the board
ETH_CLK_EN: U4.43 (P1[27]/CLKOUT/*USB_OVRCR/CAP0[1])
ETH_CRS: U4.92 (P1[8]/ENET_CRS); also elsewhere on the board
ETH_MDC: U4.87 (P1[16]/ENET_MDC); also elsewhere on the board
ETH_MDIO: U4.86 (P1[17]/ENET_MDIO); also elsewhere on the board
ETH_RST: U4.44 (P1[28]/MCOA2/PCAP1[0]/MAT0[0]); also elsewhere on the board
ETH_RXD_0: U4.91 (P1[9]/ENET_RXD0); also elsewhere on the board
ETH_RXD_1: U4.90 (P1[10]/ENET_RXD1); also elsewhere on the board
ETH_RX_ER: U4.89 (P1[14]/ENET_RX_ER); also elsewhere on the board
ETH_TXD_0: U4.95 (P1[0]/ENET_TXD0); also elsewhere on the board
ETH_TXD_1: U4.94 (P1[1]/ENET_TXD1); also elsewhere on the board
ETH_TXD_EN: U4.93 (P1[4]/ENET_TX_EN); also elsewhere on the board
ETH_X1: U4.88 (P1[15]/ENET_REF_CLK); also elsewhere on the board
FAN_1_PWM: U4.27 (P3[25]/MAT0[0]/PWM1[2]); also elsewhere on the board
FAN_2_PWM: U4.26 (P3[26]/STCLK/MAT0[1]/PWM1[3]); also elsewhere on the board
GND: C15.-, C16.2, C17.2, C18.2, C19.2, C20.2, C21.2, C22.2, C23.2, C24.2, C25.2, C26.2, SW1.1 (2), SW1.2, SW2.1 (2), SW2.2, TP6.TP, U3.1 (A0), U3.2 (A1), U3.3 (A2), U3.4 (GND), U4.11 (VSSA), U4.15 (VREFN), U4.31 (VSS_2), U4.41 (VSS_3), U4.55 (VSS_4), U4.72 (VSS_5), U4.83 (VSS_6), U4.97 (VSS), X3.2 (GND), X4.- (VBAT-); also elsewhere on the board
HMI_BUTTON_ISO_1: U4.63 (P0[16]/RXD1/SSEL0/SSEL); also elsewhere on the board
HMI_BUTTON_ISO_2: U4.62 (P0[15]/TXD1/SCK0/SCK); also elsewhere on the board
HMI_BUTTON_ISO_3: U4.61 (P0[17]/CTS1/MISO0/MISO); also elsewhere on the board
HMI_BUTTON_ISO_4: U4.60 (P0[18]/DCD1/MOSI0/MOSI); also elsewhere on the board
HMI_BUTTON_ISO_5: U4.59 (P0[19]/DSR1/SDA1); also elsewhere on the board
HMI_BUTTON_ISO_6: R14.2, R15.1; also elsewhere on the board
HMI_BUTTON_MCU_FCT_6: R15.2, U4.58 (P0[20]/DTR1/SCL1)
HMI_LCD_BACKLIGHT: U4.56 (P0[22]/RTS1/TD1); also elsewhere on the board
HMI_LCD_SCL: U4.49 (P0[11]/RXD2/SCL2/MAT3[1]); also elsewhere on the board
HMI_LCD_SDA: U4.48 (P0[10]/TXD2/SDA2/MAT3[0]); also elsewhere on the board
HMI_LED_1: U4.73 (P2[2]/PWM1[3]/CTS1/TRACEDATA[3]); also elsewhere on the board
HMI_LED_2: U4.70 (P2[3]/PWM1[4]/DCD1/TRACEDATA[2]); also elsewhere on the board
HMI_LED_3: U4.69 (P2[4]/PWM1[5]/DSR1/TRACEDATA[1]); also elsewhere on the board
HMI_LED_4: U4.68 (P2[5]/PWM1[6]/DTR1/TRACEDATA[0]); also elsewhere on the board
ISP_RXDO: U4.99 (P0[3]/RXD0/AD0[6]); also elsewhere on the board
ISP_TXDO: U4.98 (P0[2]/TXD0/AD0[7]); also elsewhere on the board
JTAG_TCK: U4.5 (TCK/SWDCLK); also elsewhere on the board
JTAG_TDI: U4.2 (TDI); also elsewhere on the board
JTAG_TDO: U4.1 (TDO/SWO); also elsewhere on the board
JTAG_TMS: U4.3 (TMS/SWDIO); also elsewhere on the board
LED_DEBUG: R20.2, U4.76 (P0[9]/I2STX_SDA/MOSI1/MAT2[3])
unnamed: R11.1, TP3.TP, U3.7 (WP)
unnamed: R17.1, R18.2, R19.2, SW2.3 (1), SW2.4 (1)
unnamed: LED1.C, R20.1
RTCX1: C19.1, U4.16 (RTCX1), X2.1
RTCX2: C24.1, U4.18 (RTCX2), X2.2
USB_D_N: U4.30 (P0[30]/USB_D?); also elsewhere on the board
USB_D_P: U4.29 (P0[29]/USB_D+); also elsewhere on the board
USB_UP_LED: U4.32 (P1[18]/USB_UP_LED/PWM1[1]/CAP1[0]); also elsewhere on the board
USB_V_BUS: U4.21 (P1[30]/VBUS/AD0[4]); also elsewhere on the board
VBAT+: U4.19 (VBAT), X4.+1 (VBAT+), X4.+2 (VBAT+)
XTAL1: U4.22 (XTAL1), X3.3 (OUT)

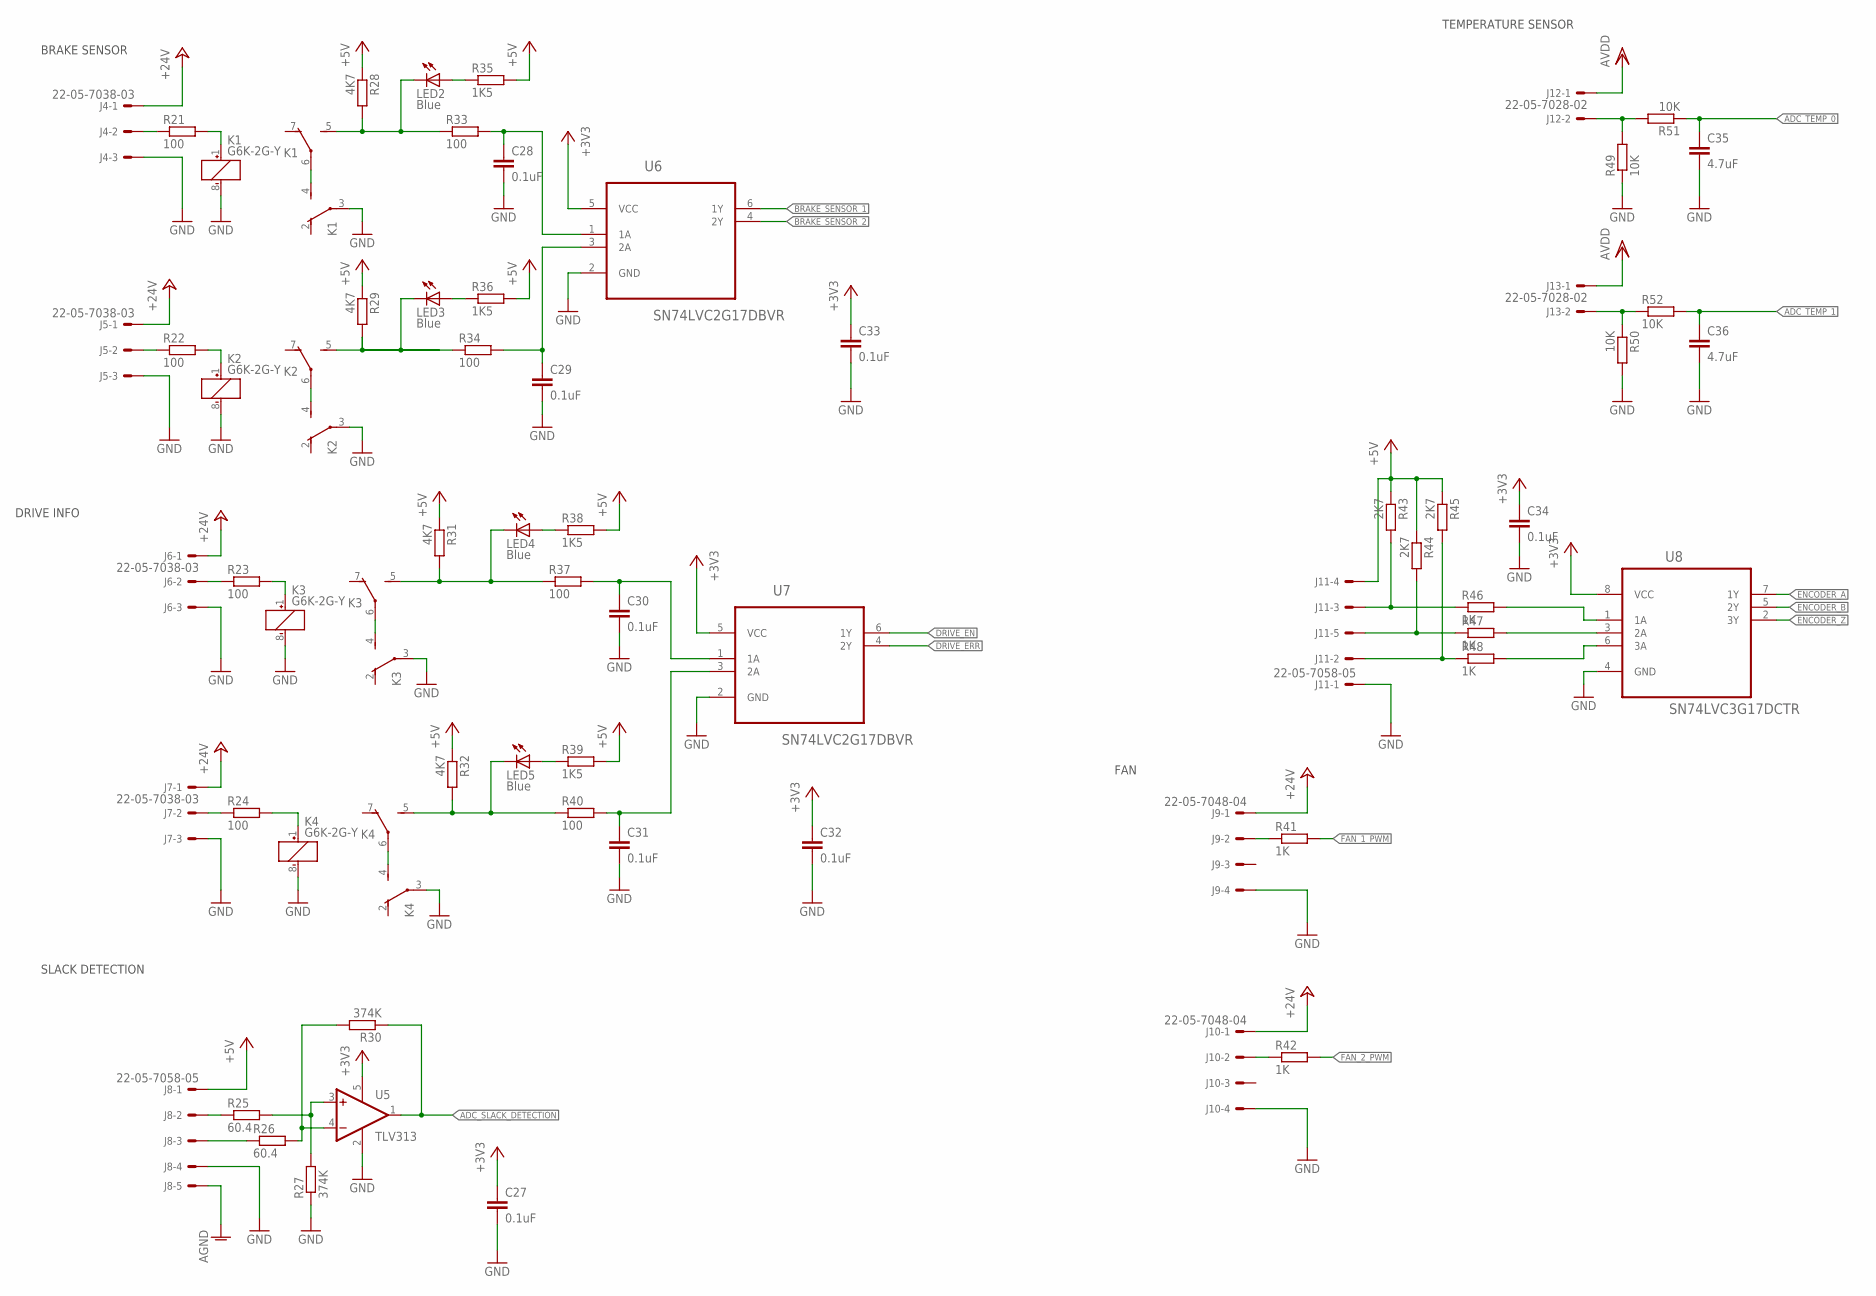
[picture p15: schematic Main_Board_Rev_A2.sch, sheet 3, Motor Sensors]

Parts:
C27, C28, C29, C30, C31, C32, C33, C34: 0.1uF; C0603; MPN MC0603B104K160CT
C35, C36: 4.7uF; C0603; MPN MC0603X475K100CT
J4, J5, J6, J7: 22-05-7038-03; 7395-03; MPN 22-05-7038
J8, J11: 22-05-7058-05; 7395-05; MPN 22-05-7058
J9, J10: 22-05-7048-04; 7395-04; MPN 22-05-7048
J12, J13: 22-05-7028-02; 7395-02; MPN 22-05-7028
K1, K2, K3, K4: G6K-2G-Y; MPN G6K-2G-YDC24 BY OMR
LED2, LED3, LED4, LED5: Blue; CHIPLED_0603; MPN OVS-0603
R21, R22, R23, R24, R33, R34, R37, R40: 100; R0603; MPN MCMR06X1000FTL
R25, R26: 60.4; R0603; MPN MCMR06X60R4FTL
R27, R30: 374K; R0603; MPN CRCW0603374KFKEA.
R28, R29, R31, R32: 4K7; R0603; MPN MCMR06X4701FTL
R35, R36, R38, R39: 1K5; R0603; MPN MCMR06X1501FTL
R41, R42, R46, R47, R48: 1K; R0603; MPN MCMR06X1001FTL
R43, R44, R45: 2K7; R0603; MPN MCMR06X2701FTL
R49, R50, R51, R52: 10K; R0603; MPN MCMR06X1002FTL
U5: TLV313; SOT23-DBV; MPN TLV313IDBVT
U6, U7: SN74LVC2G17DBVR; SOT95P280X145-6N
U8: SN74LVC3G17DCTR; SOP65P400X130-8N

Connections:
+3V3: C27.1, C32.1, C33.1, C34.1, U5.5 (V+), U6.5 (VCC), U7.5 (VCC), U8.8 (VCC); also elsewhere on the board
+5V: J8.1, J11.4, R28.1, R29.1, R31.1, R32.1, R35.2, R36.2, R38.2, R39.2, R43.1, R44.1, R45.1; also elsewhere on the board
+24V: J4.1, J5.1, J6.1, J7.1, J9.1, J10.1; also elsewhere on the board
ADC_SLACK_DETECTION: R30.1, U5.1 (OUT); also elsewhere on the board
ADC_TEMP_0: C35.1, R51.1; also elsewhere on the board
ADC_TEMP_1: C36.1, R52.2; also elsewhere on the board
AGND: J8.5; also elsewhere on the board
AVDD: J12.1, J13.1; also elsewhere on the board
BRAKE_SENSOR_1: U6.6 (1Y); also elsewhere on the board
BRAKE_SENSOR_2: U6.4 (2Y); also elsewhere on the board
DRIVE_EN: U7.6 (1Y); also elsewhere on the board
DRIVE_ERR: U7.4 (2Y); also elsewhere on the board
ENCODER_A: U8.7 (1Y); also elsewhere on the board
ENCODER_B: U8.5 (2Y); also elsewhere on the board
ENCODER_Z: U8.2 (3Y); also elsewhere on the board
FAN_1_PWM: R41.2; also elsewhere on the board
FAN_2_PWM: R42.2; also elsewhere on the board
GND: C27.2, C28.2, C29.2, C30.2, C31.2, C32.2, C33.2, C34.2, C35.2, C36.2, J4.3, J5.3, J6.3, J7.3, J8.4, J9.4, J10.4, J11.1, K1.3, K1.8 (-), K2.3, K2.8 (-), K3.3, K3.8 (-), K4.3, K4.8 (-), R27.1, R49.1, R50.2, U5.2 (V-), U6.2 (GND), U7.2 (GND), U8.4 (GND); also elsewhere on the board
unnamed: J9.2, R41.1
unnamed: J11.3, R43.2, R46.1
unnamed: J10.2, R42.1
unnamed: J11.5, R44.2, R47.1
unnamed: J4.2, R21.1
unnamed: J5.2, R22.1
unnamed: K1.1 (+), R21.2
unnamed: K3.1 (+), R23.2
unnamed: K1.4 (S), K1.6
unnamed: J6.2, R23.1
unnamed: K4.1 (+), R24.2
unnamed: J7.2, R24.1
unnamed: C29.1, R34.2, U6.3 (2A)
unnamed: C28.1, R33.2, U6.1 (1A)
unnamed: C30.1, R37.2, U7.1 (1A)
unnamed: C31.1, R40.2, U7.3 (2A)
unnamed: J11.2, R45.2, R48.1
unnamed: R48.2, U8.6 (3A)
unnamed: R47.2, U8.3 (2A)
unnamed: K2.1 (+), R22.2
unnamed: K2.4 (S), K2.6
unnamed: K1.5 (S), LED2.C, R28.2, R33.1
unnamed: K4.4 (S), K4.6
unnamed: K3.4 (S), K3.6
unnamed: R46.2, U8.1 (1A)
unnamed: J8.2, R25.1
unnamed: J12.2, R49.2, R51.2
unnamed: J13.2, R50.1, R52.1
unnamed: LED2.A, R35.1
unnamed: K2.5 (S), LED3.C, R29.2, R34.1
unnamed: LED3.A, R36.1
unnamed: K3.5 (S), LED4.C, R31.2, R37.1
unnamed: LED4.A, R38.1
unnamed: K4.5 (S), LED5.C, R32.2, R40.1
unnamed: LED5.A, R39.1
unnamed: J8.3, R26.1
unnamed: R25.2, R27.2, U5.3 (+IN)
unnamed: R26.2, R30.2, U5.4 (-IN)

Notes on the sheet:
TEMPERATURE SENSOR
BRAKE SENSOR
DRIVE INFO
FAN
SLACK DETECTION

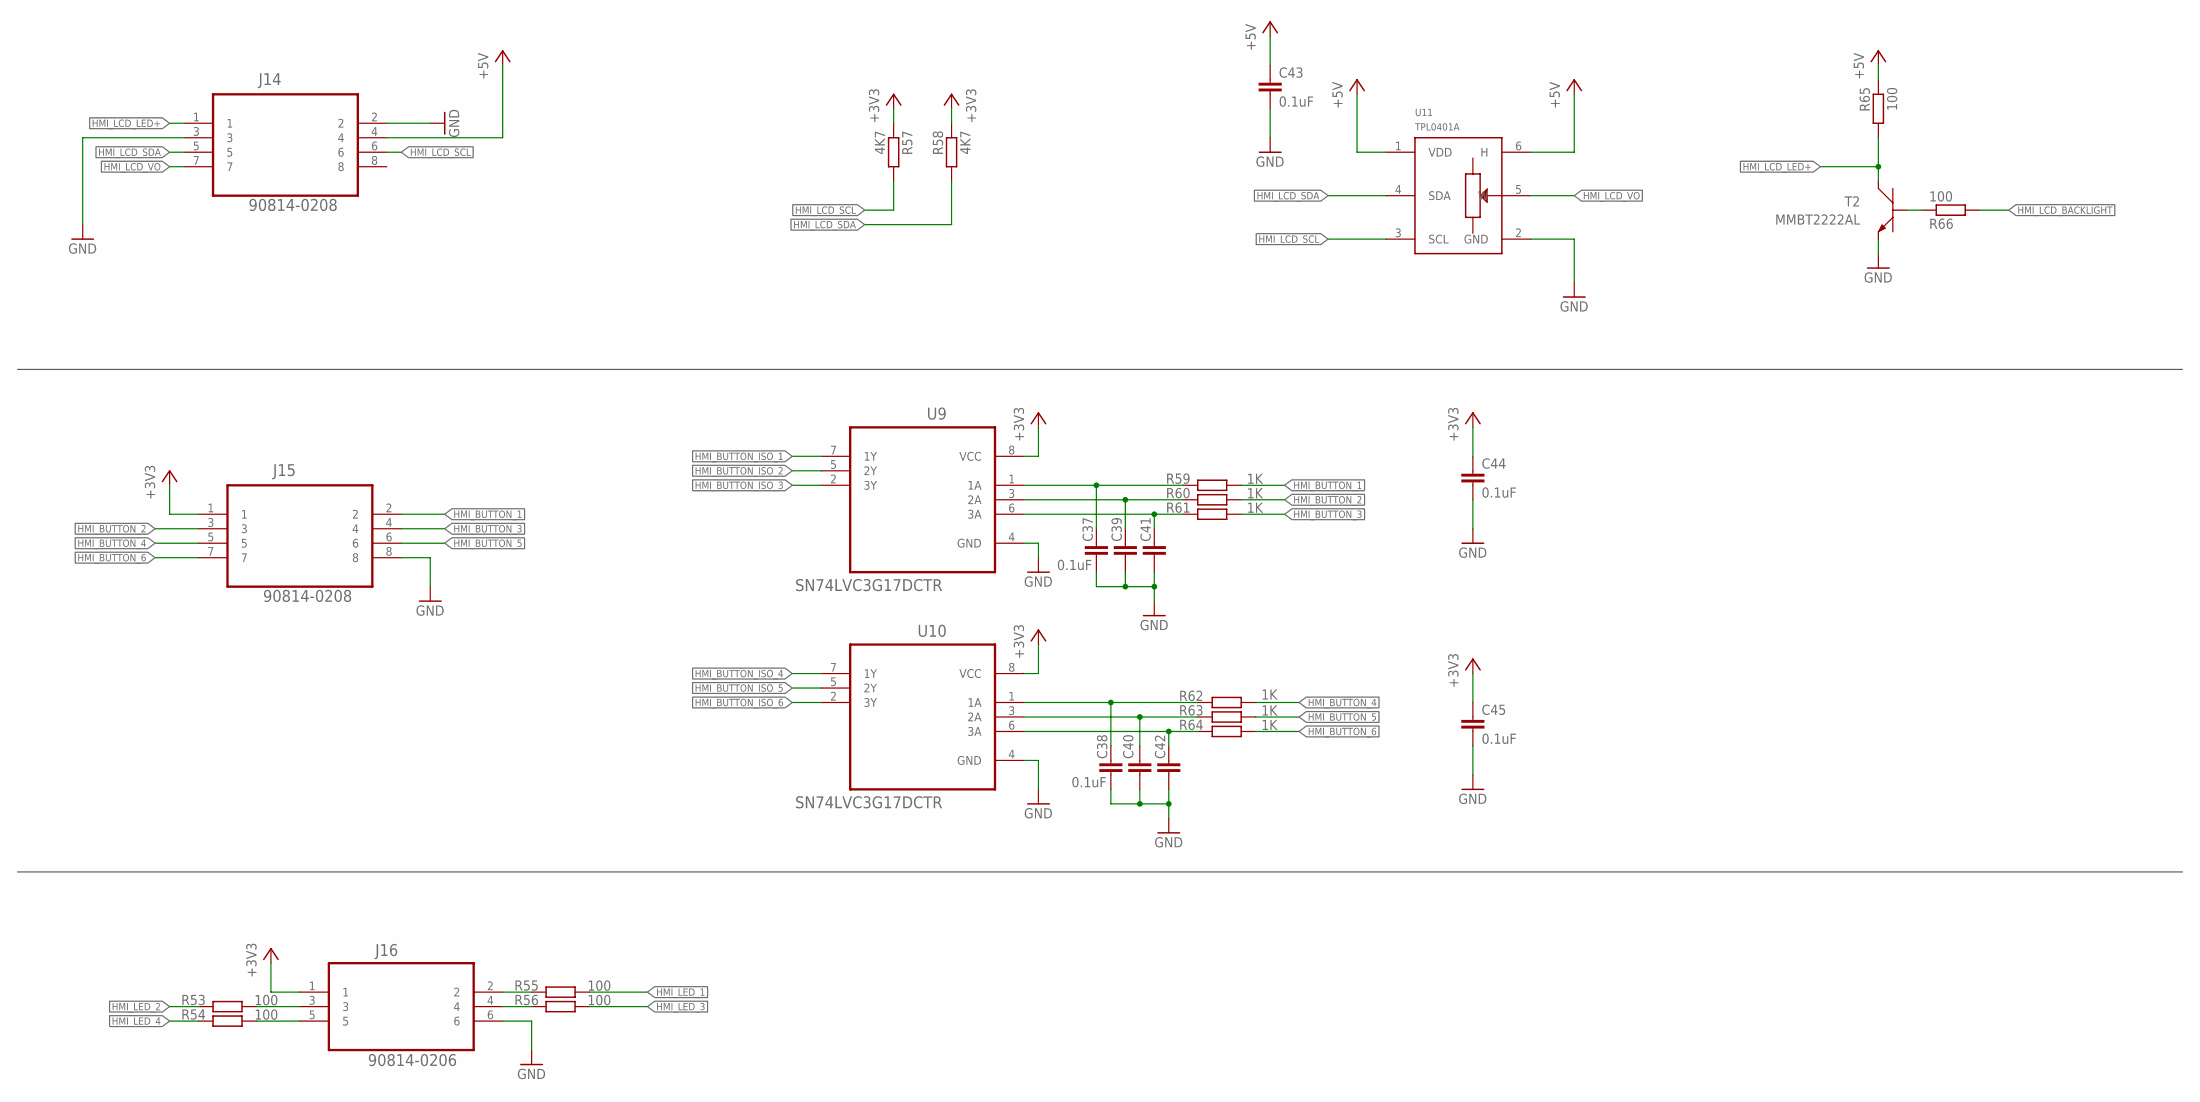
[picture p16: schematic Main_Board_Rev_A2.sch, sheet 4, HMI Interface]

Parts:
C37, C38, C39, C40, C41, C42, C43, C44, C45: 0.1uF; C0603; MPN MC0603B104K160CT
J14, J15: 90814-0208; MOLEX_90814-0208
J16: 90814-0206; MOLEX_90814-0206
R53, R54, R55, R56, R65, R66: 100; R0603; MPN MCMR06X1000FTL
R57, R58: 4K7; R0603; MPN MCMR06X4701FTL
R59, R60, R61, R62, R63, R64: 1K; R0603; MPN MCMR06X1001FTL
T2: MMBT2222AL; SOT−23; MPN MMBT2222ALT3G
U9, U10: SN74LVC3G17DCTR; SOP65P400X130-8N
U11: TPL0401A; SC-70-DCK; MPN ISL90727WIE627Z-T7A

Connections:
+3V3: C44.1, C45.1, J15.1, J16.1, R57.1, R58.1, U9.8 (VCC), U10.8 (VCC); also elsewhere on the board
+5V: C43.1, J14.4, R65.1, U11.1 (VDD), U11.6 (H); also elsewhere on the board
GND: C37.2, C38.2, C39.2, C40.2, C41.2, C42.2, C43.2, C44.2, C45.2, J14.2, J14.3, J15.8, J16.6, T2.2 (E), U9.4 (GND), U10.4 (GND), U11.2 (GND); also elsewhere on the board
HMI_BUTTON_1: J15.2, R59.1
HMI_BUTTON_2: J15.3, R60.1
HMI_BUTTON_3: J15.4, R61.1
HMI_BUTTON_4: J15.5, R62.1
HMI_BUTTON_5: J15.6, R63.1
HMI_BUTTON_6: J15.7, R64.1
HMI_BUTTON_ISO_1: U9.7 (1Y); also elsewhere on the board
HMI_BUTTON_ISO_2: U9.5 (2Y); also elsewhere on the board
HMI_BUTTON_ISO_3: U9.2 (3Y); also elsewhere on the board
HMI_BUTTON_ISO_4: U10.7 (1Y); also elsewhere on the board
HMI_BUTTON_ISO_5: U10.5 (2Y); also elsewhere on the board
HMI_BUTTON_ISO_6: U10.2 (3Y); also elsewhere on the board
HMI_LCD_BACKLIGHT: R66.2; also elsewhere on the board
HMI_LCD_LED+: J14.1, R65.2, T2.3 (C)
HMI_LCD_SCL: J14.6, R57.2, U11.3 (SCL); also elsewhere on the board
HMI_LCD_SDA: J14.5, R58.2, U11.4 (SDA); also elsewhere on the board
HMI_LCD_VO: J14.7, U11.5 (W)
HMI_LED_1: R55.1; also elsewhere on the board
HMI_LED_2: R53.2; also elsewhere on the board
HMI_LED_3: R56.1; also elsewhere on the board
HMI_LED_4: R54.2; also elsewhere on the board
unnamed: J16.3, R53.1
unnamed: J16.5, R54.1
unnamed: C37.1, R59.2, U9.1 (1A)
unnamed: C39.1, R60.2, U9.3 (2A)
unnamed: C41.1, R61.2, U9.6 (3A)
unnamed: C38.1, R62.2, U10.1 (1A)
unnamed: C40.1, R63.2, U10.3 (2A)
unnamed: C42.1, R64.2, U10.6 (3A)
unnamed: J16.2, R55.2
unnamed: J16.4, R56.2
unnamed: R66.1, T2.1 (B)

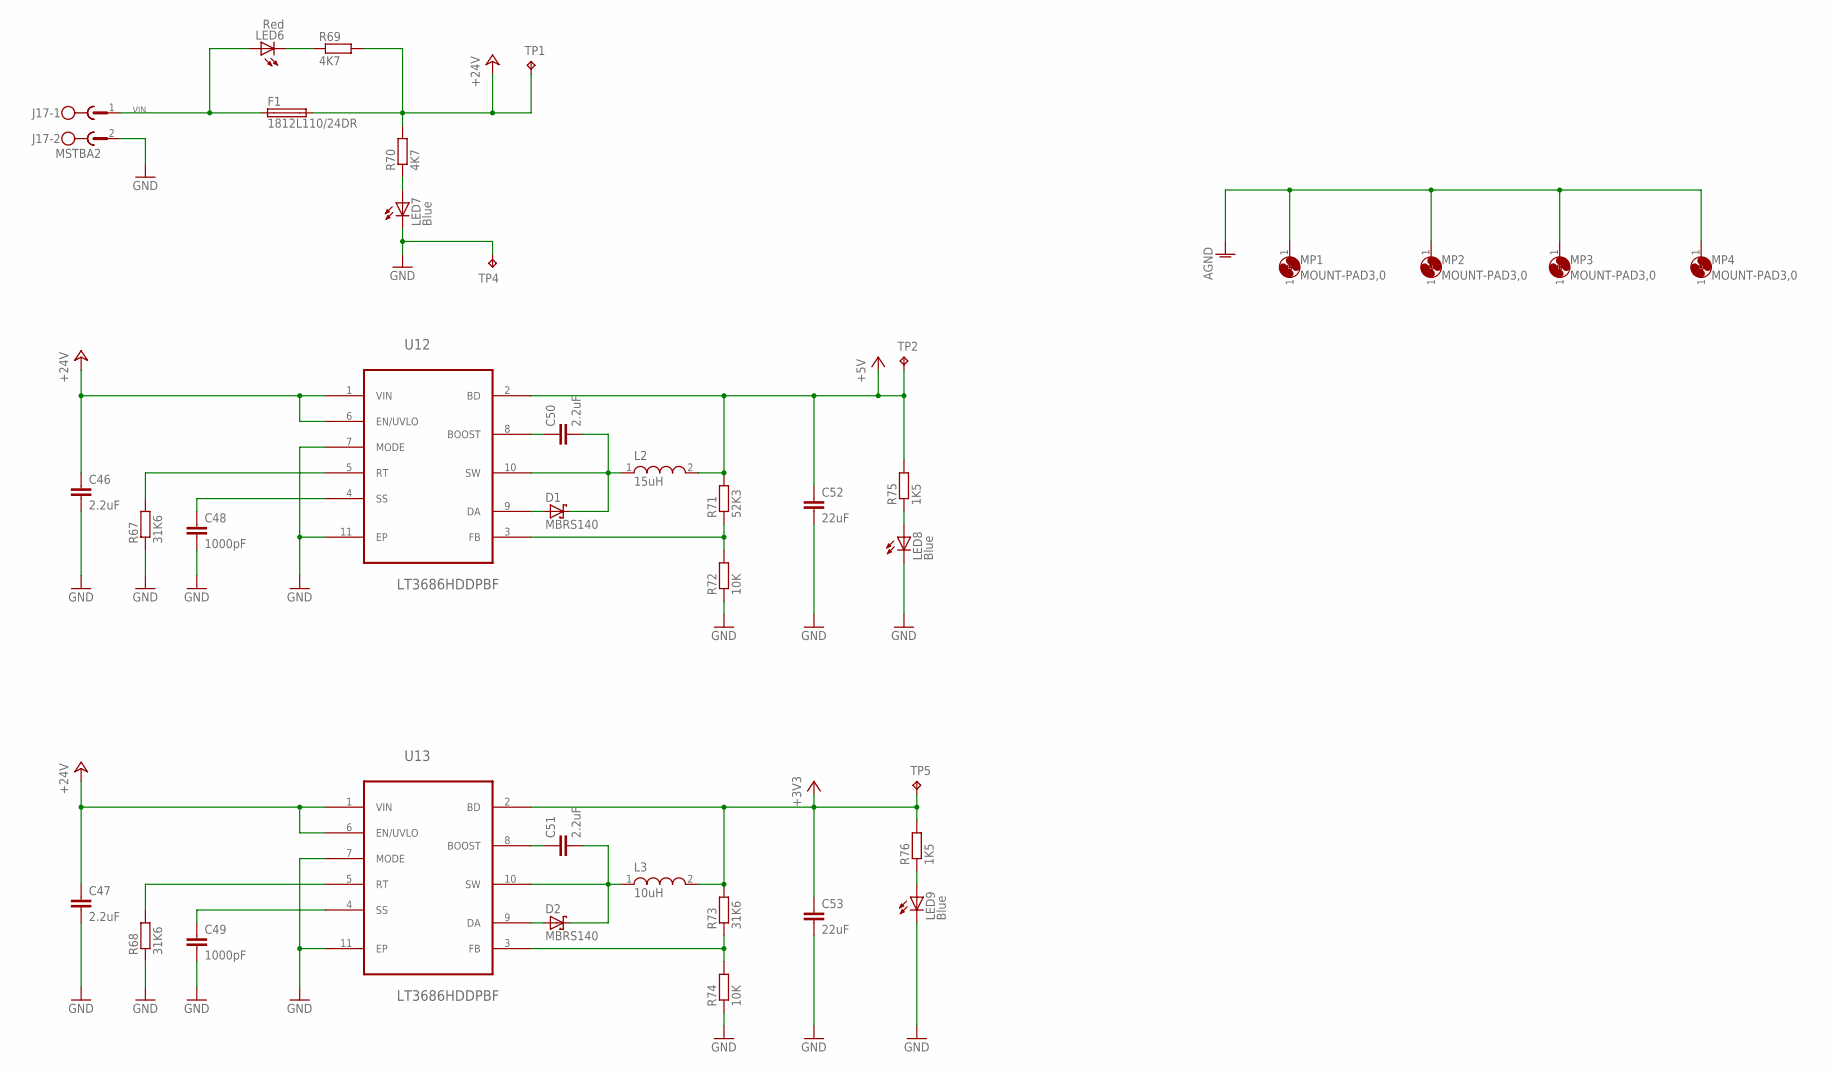
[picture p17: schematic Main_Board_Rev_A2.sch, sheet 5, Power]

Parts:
C46, C47, C50, C51: 2.2uF; C0603; MPN GRT188R61H225KE13D
C48, C49: 1000pF; C0603; MPN MC0603B102K500CT
C52, C53: 22uF; C0805; MPN MC0805X226M6R3CT
D1, D2: MBRS140; DO-214AA; MPN MBRS140T3G
F1: 1812L110/24DR; LITTLEFUSE_SMD; MPN 3557
J17: MSTBA2
L2: 15uH; WE-PD2_5848/5820; MPN 744774115
L3: 10uH; WE-PD2_5848/5820; MPN 74477410
LED6: Red; CHIPLED_0603; MPN OVS-0608
LED7, LED8, LED9: Blue; CHIPLED_0603; MPN OVS-0603
MP1, MP2, MP3, MP4: MOUNT-PAD3,0; P3,0
R67, R68, R73: 31K6; R0603; MPN MC0603SAF3162T5E
R69, R70: 4K7; R0603; MPN MCMR06X4701FTL
R71: 52K3; R0603; MPN MC0063W0603152K3
R72, R74: 10K; R0603; MPN MCMR06X1002FTL
R75, R76: 1K5; R0603; MPN MCMR06X1501FTL
TP1, TP2, TP4, TP5: TPB1,27; B1,27
U12, U13: LT3686HDDPBF; DFN300X300X80-11N

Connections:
+3V3: C53.1, L3.2, R73.2, R76.2, TP5.TP, U13.2 (BD); also elsewhere on the board
+5V: C52.1, L2.2, R71.2, R75.2, TP2.TP, U12.2 (BD); also elsewhere on the board
+24V: C46.1, C47.1, F1.2, R69.2, R70.2, TP1.TP, U12.1 (VIN), U12.6 (EN/UVLO), U13.1 (VIN), U13.6 (EN/UVLO); also elsewhere on the board
AGND: MP1.1, MP2.1, MP3.1, MP4.1; also elsewhere on the board
GND: C46.2, C47.2, C48.2, C49.2, C52.2, C53.2, J17.2, LED7.C, LED8.C, LED9.C, R67.1, R68.1, R72.1, R74.1, TP4.TP, U12.7 (MODE), U12.11 (EP), U13.7 (MODE), U13.11 (EP); also elsewhere on the board
unnamed: R67.2, U12.5 (RT)
unnamed: C48.1, U12.4 (SS)
unnamed: R68.2, U13.5 (RT)
unnamed: C49.1, U13.4 (SS)
unnamed: R71.1, R72.2, U12.3 (FB)
unnamed: C50.1, U12.8 (BOOST)
unnamed: C50.2, D1.C, L2.1, U12.10 (SW)
unnamed: D1.A, U12.9 (DA)
unnamed: R73.1, R74.2, U13.3 (FB)
unnamed: C51.1, U13.8 (BOOST)
unnamed: C51.2, D2.C, L3.1, U13.10 (SW)
unnamed: LED7.A, R70.1
unnamed: LED6.C, R69.1
unnamed: D2.A, U13.9 (DA)
unnamed: LED9.A, R76.1
unnamed: LED8.A, R75.1
VIN: F1.1, J17.1, LED6.A

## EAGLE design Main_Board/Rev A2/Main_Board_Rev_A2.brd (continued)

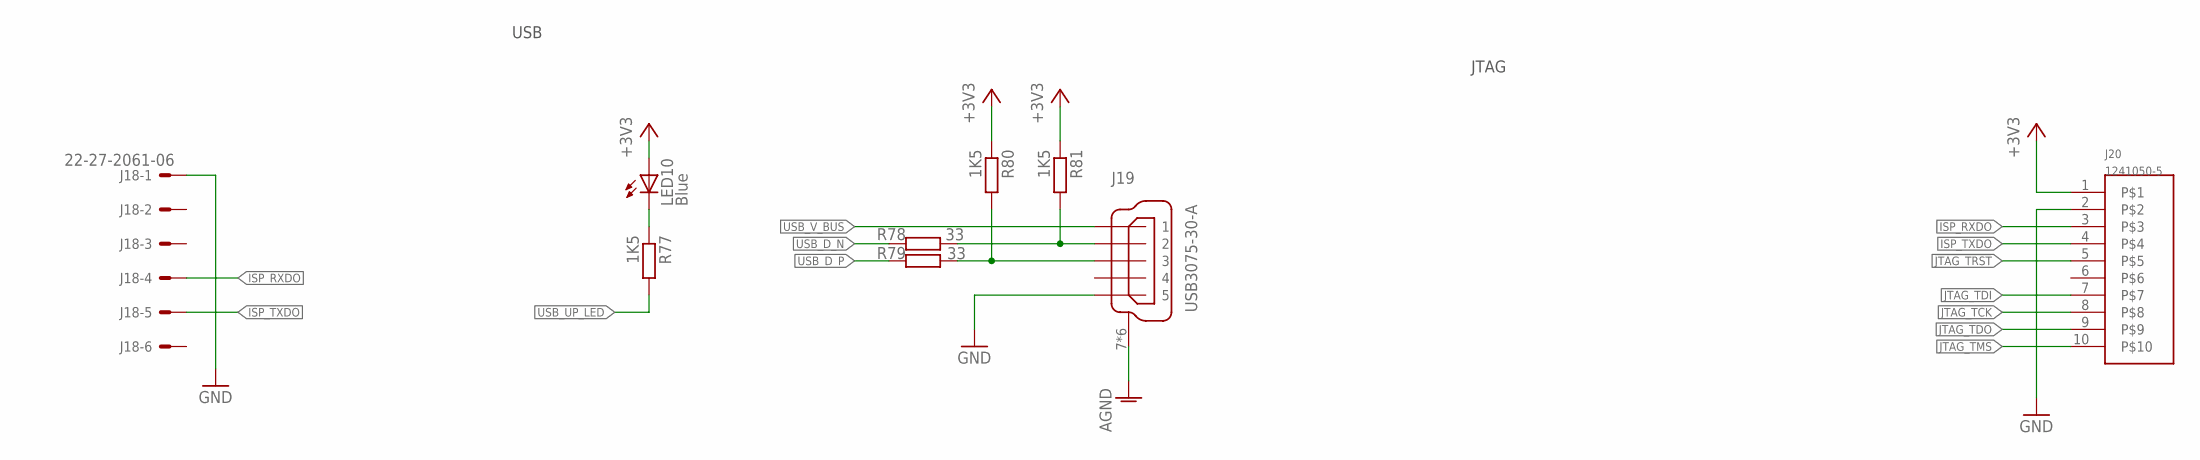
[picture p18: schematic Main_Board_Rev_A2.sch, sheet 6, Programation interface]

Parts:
J18: 22-27-2061-06; 6410-06; MPN 22-27-2061
J19: USB3075-30-A; USB_MICROB_SMT; MPN USB3075-30-A
J20: 1241050-5; 2.54/2X5; MPN 1241050-5
LED10: Blue; CHIPLED_0603; MPN OVS-0603
R77, R80, R81: 1K5; R0603; MPN MCMR06X1501FTL
R78, R79: 33; R0603; MPN MCMR06X33R0FTL

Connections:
!JTAG_TRST: J20.5; also elsewhere on the board
+3V3: J20.1, LED10.A, R80.1, R81.1; also elsewhere on the board
AGND: J19.7 (S), J19.8 (S), J19.9 (S), J19.10 (S), J19.11 (S), J19.12 (S); also elsewhere on the board
GND: J18.1, J19.5, J20.2; also elsewhere on the board
ISP_RXDO: J18.4, J20.3; also elsewhere on the board
ISP_TXDO: J18.5, J20.4; also elsewhere on the board
JTAG_TCK: J20.8; also elsewhere on the board
JTAG_TDI: J20.7; also elsewhere on the board
JTAG_TDO: J20.9; also elsewhere on the board
JTAG_TMS: J20.10; also elsewhere on the board
unnamed: J19.2, R78.1, R81.2
unnamed: J19.3, R79.1, R80.2
unnamed: LED10.C, R77.1
USB_D_N: R78.2; also elsewhere on the board
USB_D_P: R79.2; also elsewhere on the board
USB_UP_LED: R77.2; also elsewhere on the board
USB_V_BUS: J19.1; also elsewhere on the board

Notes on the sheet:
USB
JTAG

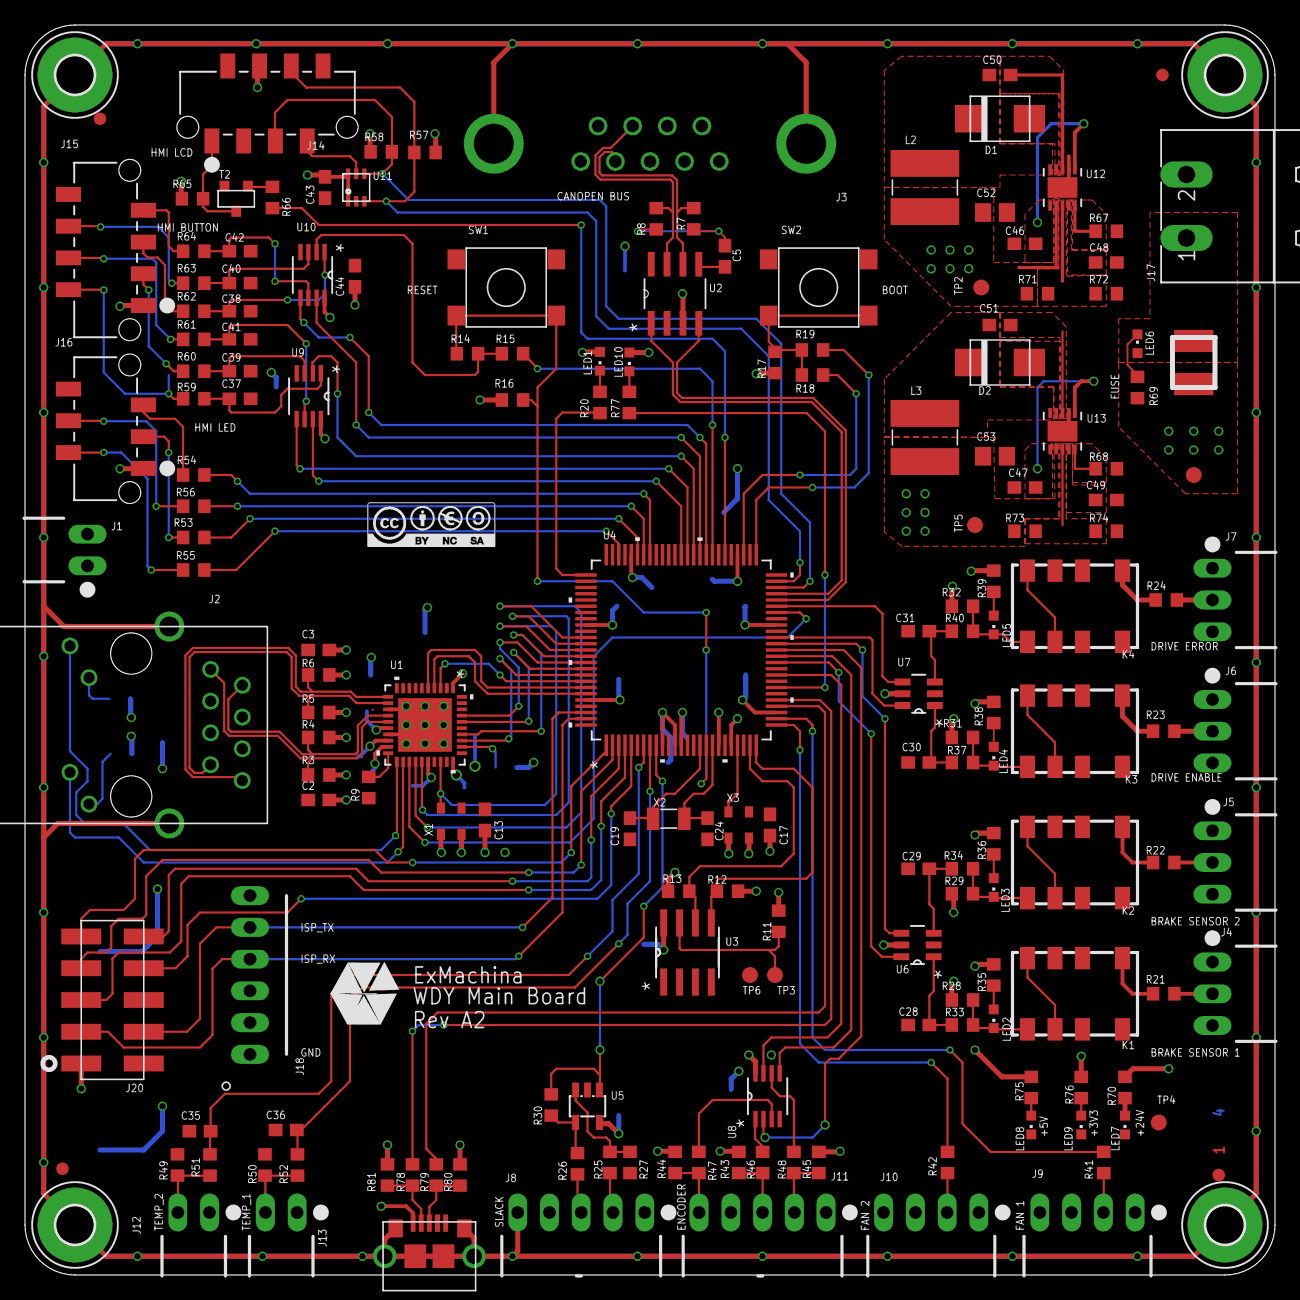
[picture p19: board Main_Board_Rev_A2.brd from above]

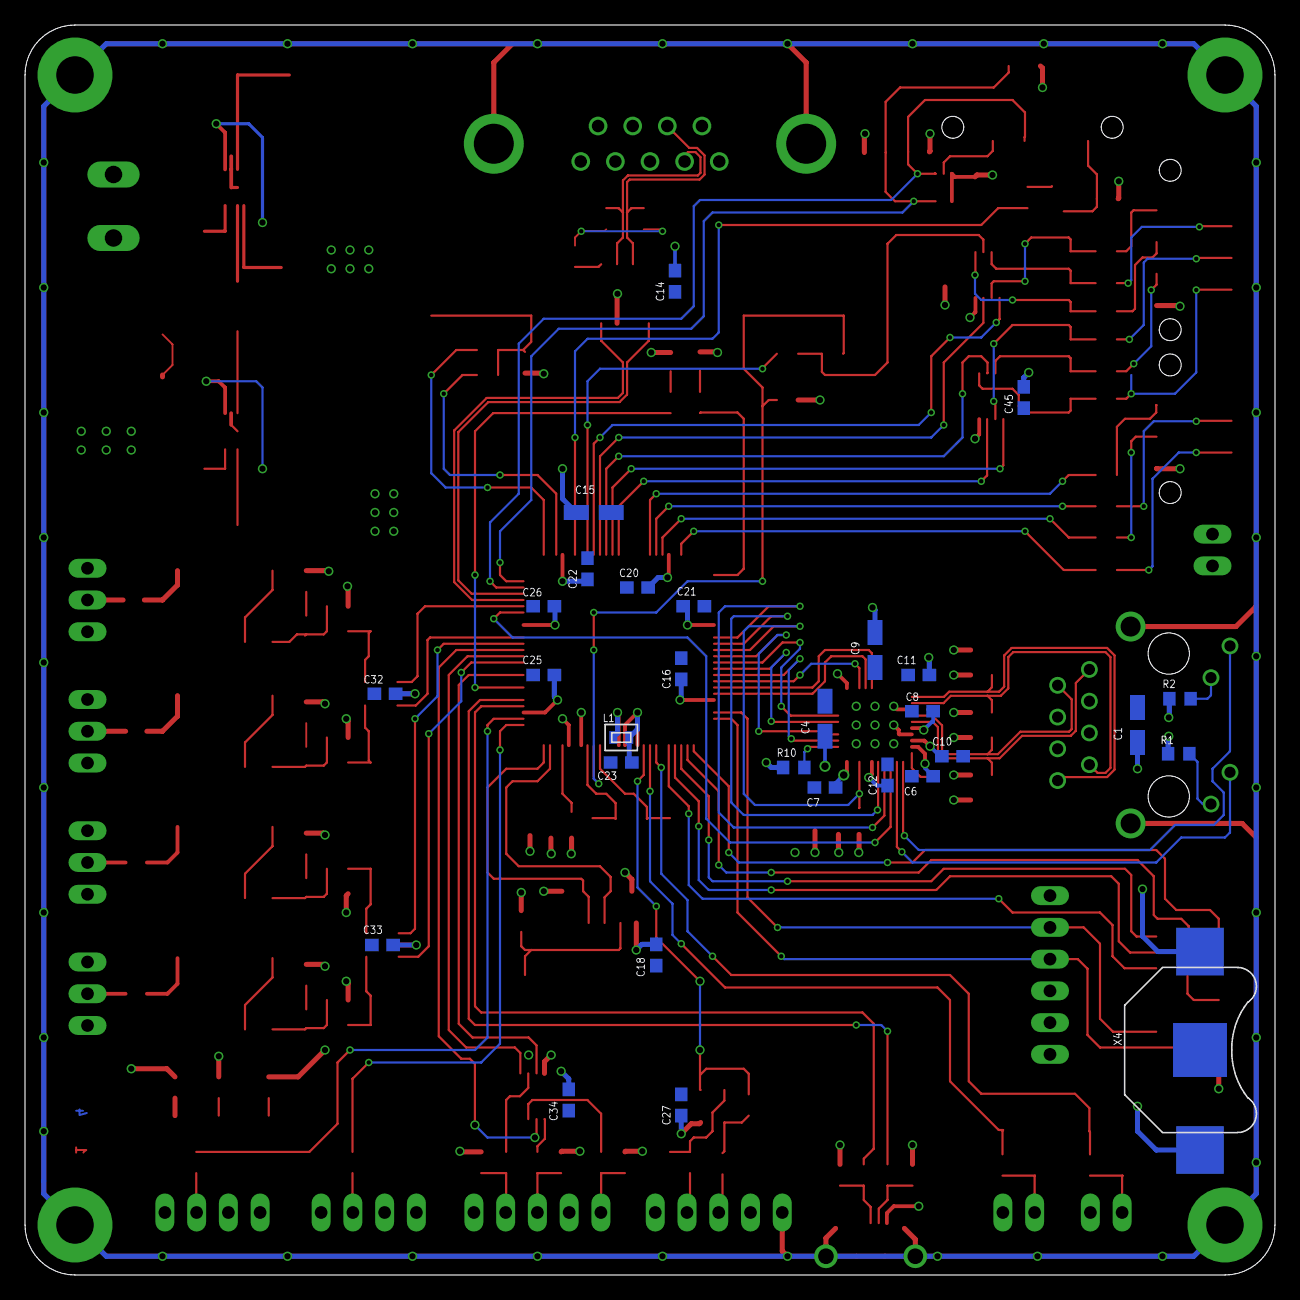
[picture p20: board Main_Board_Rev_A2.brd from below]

Board: 4 copper layers, 100.0 x 100.0 mm, 210 parts (29 on the bottom side), 161 nets.

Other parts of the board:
U$1: CC-BY-NC-SA

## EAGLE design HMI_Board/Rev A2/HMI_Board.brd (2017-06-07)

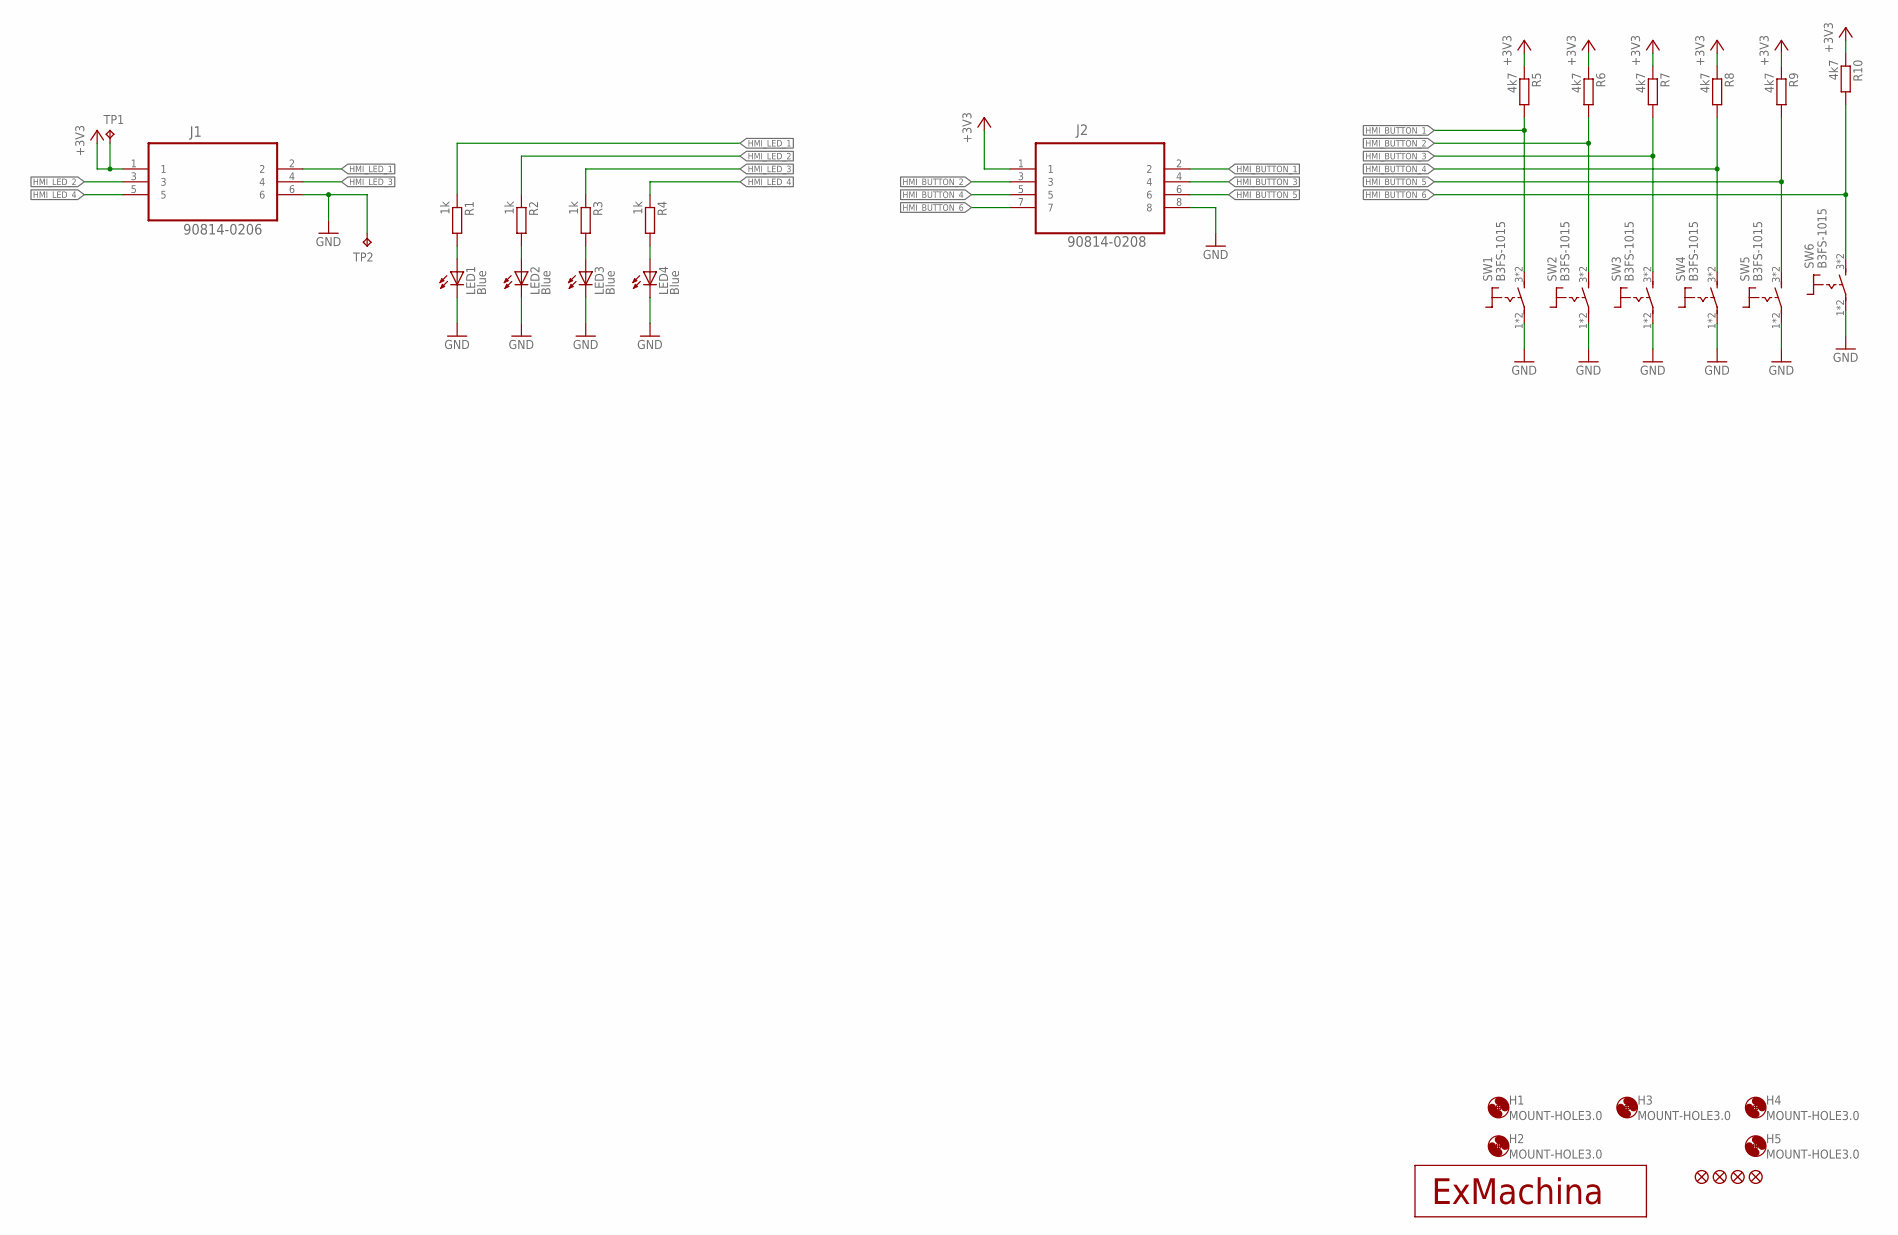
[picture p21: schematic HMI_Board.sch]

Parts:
H1, H2, H3, H4, H5: MOUNT-HOLE3.0; 3,0
J1: 90814-0206; MOLEX_90814-0206
J2: 90814-0208; MOLEX_90814-0208
JP1, JP2, JP3, JP4: FIDUCIAL1X2; FIDUCIAL-1X2
LED1, LED2, LED3, LED4: Blue; SML0603
R1, R2, R3, R4: 1k; R0603
R5, R6, R7, R8, R9, R10: 4k7; R0603
SW1, SW2, SW3, SW4, SW5, SW6: B3FS-1015; B3FS
T1: EXMACHINA-LOGO-NAME; EXM-LOGO-BASELINE
TP1, TP2: TPB2,54; B2,54

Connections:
+3V3: J1.1, J2.1, R5.1, R6.1, R7.1, R8.1, R9.1, R10.1, TP1.TP
GND: J1.6, J2.8, LED1.C, LED2.C, LED3.C, LED4.C, SW1.1 (2), SW1.2, SW2.1 (2), SW2.2, SW3.1 (2), SW3.2, SW4.1 (2), SW4.2, SW5.1 (2), SW5.2, SW6.1 (2), SW6.2, TP2.TP
HMI_BUTTON_1: J2.2, R5.2, SW1.3 (1), SW1.4 (1)
HMI_BUTTON_2: J2.3, R6.2, SW2.3 (1), SW2.4 (1)
HMI_BUTTON_3: J2.4, R7.2, SW3.3 (1), SW3.4 (1)
HMI_BUTTON_4: J2.5, R8.2, SW4.3 (1), SW4.4 (1)
HMI_BUTTON_5: J2.6, R9.2, SW5.3 (1), SW5.4 (1)
HMI_BUTTON_6: J2.7, R10.2, SW6.3 (1), SW6.4 (1)
HMI_LED_1: J1.2, R1.1
HMI_LED_2: J1.3, R2.1
HMI_LED_3: J1.4, R3.1
HMI_LED_4: J1.5, R4.1
unnamed: LED1.A, R1.2
unnamed: LED2.A, R2.2
unnamed: LED3.A, R3.2
unnamed: LED4.A, R4.2

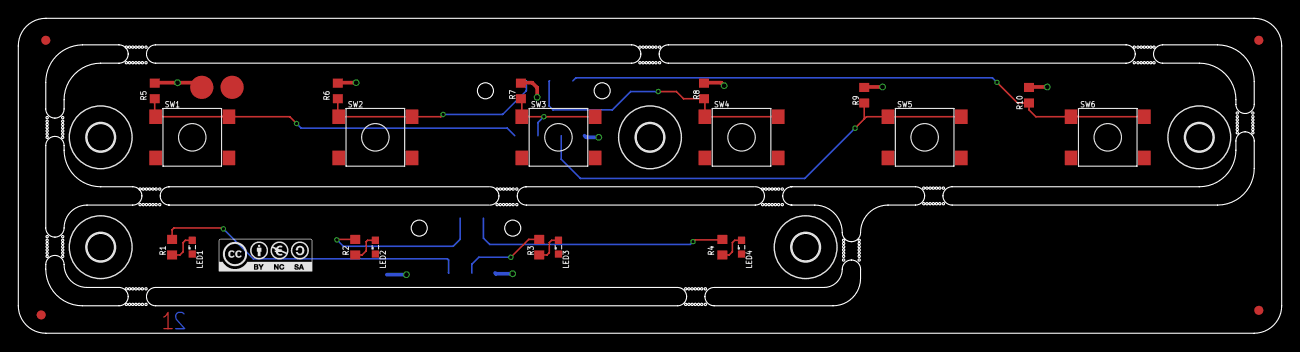
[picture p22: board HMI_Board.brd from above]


Board: 2 copper layers, 138.0 x 34.4 mm, 37 parts (5 on the bottom side), 16 nets.

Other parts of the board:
U$2: EXMACHINA-LOGO-NAME; EXM-LOGO-BASELINE
U$3, U$4: CC-BY-NC-SA

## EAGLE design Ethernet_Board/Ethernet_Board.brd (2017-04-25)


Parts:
C1: 4.7uF; CT3216; MPN F931A475MAA
C2, C3, C5, C6, C7, C9, C10, C11, C12: 100nF; C0603; MPN MC0603B104K250CT
C4, C8: 10uF; CT3216; MPN F931A106MAA
D1: STPS3L40UF; SMB
H1, H2, H3, H4: MOUNT-HOLE3.0; 3,0
J1: 22-05-7028-02; 7395-02; MPN 22-05-7028
J2, J3: 22-05-7068-06; 7395-06; MPN 22-05-7068
JP1, JP2, JP3, JP4: FIDUCIAL1X2; FIDUCIAL-1X2
P1: RB1-125BAG1A; WIZNET_RB1-125BAG1A
R1, R2: 220; R0603; MPN MCMR06X2200FTL
R3, R4, R5, R6: 49.9; R0603; MPN MCMR06X49R9FTL
R7: 4K7; R0603; MPN MCMR06X4701FTL
R8: 2K2; R0603; MPN MCMR06X2201FTL
T1: EXMACHINA-LOGO-NAME; EXM-LOGO-BASELINE
U1: DP83848JSQ/NOPB; SQA40B; MPN DP83848JSQ/NOPB
X1: ASE_50; ASE; MPN ASE-50.000MHZ-LC-T

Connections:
+3V3: C1.+, C2.1, C3.1, C8.+, C9.1, C10.1, C11.1, C12.1, D1.C, J1.1, P1.R3 (CT), R1.2, R2.2, R3.1, R4.1, R5.1, R6.1, R8.1, U1.1 (IOVDD33_2), U1.18 (AVDD33), U1.26 (IOVDD33), X1.1 (TRI), X1.4 (VDD)
ETH_CRS: J2.3, U1.33 (CRS/CRS_DV/LED_CFG)
ETH_MDC: J2.4, U1.25 (MDC)
ETH_MDIO: J2.5, U1.24 (MDIO)
ETH_RST: J2.6, U1.23 (RESET_N)
ETH_RXD_0: J3.5, U1.36 (RXD_0/PHYAD1)
ETH_RXD_1: J3.4, U1.37 (RXD_1/PHYAD2)
ETH_RX_ER: J3.6, U1.34 (RX_ER/MDIX_EN)
ETH_RX_N: P1.R8 (RD-), R6.2, U1.11 (RD-)
ETH_RX_P: P1.R7 (RD+), R5.2, U1.12 (RD+)
ETH_TXD_0: J3.2, U1.4 (TXD_0)
ETH_TXD_1: J3.1, U1.5 (TXD_1)
ETH_TXD_EN: J3.3, U1.3 (TX_EN)
ETH_TX_N: P1.R2 (TD-), R4.2, U1.14 (TD-)
ETH_TX_P: P1.R1 (TD+), R3.2, U1.15 (TD+)
ETH_X1: J2.1, U1.28 (X1), X1.3 (OUT)
GND: C1.-, C2.2, C3.2, C4.-, C5.2, C6.2, C7.2, C8.-, C9.2, C10.2, C11.2, C12.2, D1.A, J1.2, J2.2, P1.R4, P1.R5, P1.R6, R7.2, U1.13 (AGND_2), U1.17 (AGND), U1.29 (DGND), U1.40 (IOGND), U1.41 (DAP), X1.2 (GND)
L1_1: P1.L2, U1.22 (LED_LINK/AN0)
L1_2: P1.L4, U1.21 (LED_SPEED/AN1)
MII_MODE: R8.2, U1.32 (RX_DV/MII_MODE)
unnamed: R7.1, U1.20 (RBIAS)
unnamed: P1.L1, R1.1
unnamed: P1.L3, R2.1
PFBOUT: C4.+, C5.1, C6.1, C7.1, U1.16 (PFBIN1), U1.19 (PFBOUT), U1.30 (PFBIN2)

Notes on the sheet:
ETHERNET INPUT
ETHERNETPHI



Board: 4 copper layers, 57.0 x 41.0 mm, 36 parts (8 on the bottom side), 24 nets.

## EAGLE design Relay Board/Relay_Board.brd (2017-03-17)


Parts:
C1, C2, C3, C4, C5, C6: 0.1uF; C0603; MPN MC0603B104K250CT
D1, D2, D3, D4: STPS3L40UF; SMB
H1, H2, H3, H4: MOUNT-HOLE3.0; 3,0
J1, J2: 22-05-7038-03; 7395-03; MPN 22-05-7038
J3, J4, J6, J7: 22-05-7028-02; 7395-02; MPN 22-05-7028
J5: 22-05-7048-04; 7395-04; MPN 22-05-7048
JP1, JP2, JP3, JP4: FIDUCIAL1X2; FIDUCIAL-1X2
K1, K2, K3, K4: G6K-2G-Y; MPN G6K-2G-Y 24DC
LED1, LED2, LED3, LED4: Blue; CHIPLED_0603; MPN OVS-0603
R1, R2, R3, R4, R9, R10, R13, R16: 100; R0603; MPN MCMR06X1000FTL
R5, R6, R7, R8: 4K7; R0603; MPN MCMR06X4701FTL
R11, R12, R14, R15: 1K5; R0603; MPN MCMR06X1501FTL
T1: EXMACHINA-LOGO-NAME; EXM-LOGO-BASELINE
U1, U2: SN74LVC2G17DBVR; SOT95P280X145-6N
X1: MSTBA2

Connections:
+3V3: C5.1, C6.1, J7.1, U1.5 (VCC), U2.5 (VCC)
+5V: J6.1, R5.1, R6.1, R7.1, R8.1, R11.2, R12.2, R14.2, R15.2
+24V: J1.1, J2.1, J3.1, J4.1, X1.1
BRAKE_SENSOR_1: J5.1, U1.6 (1Y)
BRAKE_SENSOR_2: J5.2, U1.4 (2Y)
DRIVE_EN: J5.3, U2.6 (1Y)
DRIVE_ERR: J5.4, U2.4 (2Y)
GND: C1.2, C2.2, C3.2, C4.2, C5.2, C6.2, D1.A, D2.A, D3.A, D4.A, J1.3, J2.3, J6.2, J7.2, K1.3, K1.8 (-), K2.3, K2.8 (-), K3.3, K3.8 (-), K4.3, K4.8 (-), U1.2 (GND), U2.2 (GND), X1.2
unnamed: J1.2, R1.1
unnamed: J2.2, R2.1
unnamed: D1.C, K1.1 (+), R1.2
unnamed: D3.C, K3.1 (+), R3.2
unnamed: K1.4 (S), K1.6
unnamed: J3.2, R3.1
unnamed: D4.C, K4.1 (+), R4.2
unnamed: J4.2, R4.1
unnamed: C2.1, R10.2, U1.3 (2A)
unnamed: C1.1, R9.2, U1.1 (1A)
unnamed: C3.1, R13.2, U2.1 (1A)
unnamed: C4.1, R16.2, U2.3 (2A)
unnamed: D2.C, K2.1 (+), R2.2
unnamed: K2.4 (S), K2.6
unnamed: K1.5 (S), LED1.C, R5.2, R9.1
unnamed: K4.4 (S), K4.6
unnamed: K3.4 (S), K3.6
unnamed: LED1.A, R11.1
unnamed: K2.5 (S), LED2.C, R6.2, R10.1
unnamed: LED2.A, R12.1
unnamed: K3.5 (S), LED3.C, R7.2, R13.1
unnamed: LED3.A, R14.1
unnamed: K4.5 (S), LED4.C, R8.2, R16.1
unnamed: LED4.A, R15.1

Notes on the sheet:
BRAKE SENSOR
DRIVE INFO


Board: 2 copper layers, 57.0 x 41.0 mm, 53 parts (0 on the bottom side), 32 nets.

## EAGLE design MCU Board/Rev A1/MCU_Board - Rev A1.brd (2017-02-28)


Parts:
C1: 10uF; CT3216; MPN F931A106MAA
C2, C3, C4, C6, C7, C8, C9, C11, C12: 0.1uF; C0603; MPN MC0603B104K160CT
C5, C10: 18pF; C0603; MPN MC0603N180K500CT
JP1: BC-2-P
JP2, JP3, JP4, JP5: FIDUCIAL1X2; FIDUCIAL-1X2
L1: 0603PS-103KLB; 0603
LED1: Blue; CHIPLED_0603; MPN OVS-0603
R1, R2, R3: 4K7; R0603; MPN MCMR06X4701FTL
R4, R5, R8, R9: 0R; R0603; MPN MCMR06X000 PTL
R6, R7: 10K; R0603; MPN MCMR06X1002FTL
R10: 1K5; R0603; MPN MCMR06X1501FTL
SW1, SW2: B3FS-1015; B3FS
T2: EXMACHINA-LOGO-NAME; EXM-LOGO-BASELINE
U1: AT24C512C-SSHM-B; SOIC127P600X175-8N
U2: LPC1768FBD100; SOT407-1; MPN LPC1768FBD100
X1: FC-135; MPN Q13FC13500004
X2: ASE-12; ASE; MPN ASE-12.000MHZ-LC-T
X3: 3000; MPN 3000

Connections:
!RESET: U2.17 (*RESET)
+3V3: C1.+, C2.1, C3.1, C4.1, C6.1, C7.1, C8.1, C11.1, C12.1, L1.P$1 (1), R1.2, R2.2, R3.2, R6.2, R7.2, U1.8 (VCC), U2.13 (NC), U2.28 (VDD_2), U2.42 (VDD_3), U2.54 (VDD_4), U2.71 (VDD_5), U2.84 (VDD_6), U2.96 (VDD), X2.1 (TRI), X2.4 (VDD); also elsewhere on the board
ADC_SLACK_DETECTION: U2.7 (P0[25]/AD0[2]/I2SRX_SDA/TXD3); also elsewhere on the board
ADC_TEMP_0: U2.9 (P0[23]/AD0[0]/I2SRX_CLK/CAP3[0]); also elsewhere on the board
ADC_TEMP_1: U2.8 (P0[24]/AD0[1]/I2SRX_WS/CAP3[1]); also elsewhere on the board
AVDD: C9.1, L1.P$2 (2), U2.10 (VDDA), U2.12 (VREFP); also elsewhere on the board
BOOT_SELECT_P2_10: R8.1, U2.53 (P2[10]/*EINT0/NMI)
BOOT_SELECT_P2_12: R9.1, U2.51 (P2[12]/*EINT2/I2STX_WS)
BRAKE_SENSOR_1: U2.81 (P0[4]/I2SRX_CLK/RD2/CAP2[0]); also elsewhere on the board
BRAKE_SENSOR_2: U2.80 (P0[5]/I2SRX_WS/TD2/CAP2[1]); also elsewhere on the board
CAN_RX: U2.46 (P0[0]/RD1/TXD3/SDA1); also elsewhere on the board
CAN_TX: U2.47 (P0[1]/TD1/RXD3/SCL1); also elsewhere on the board
DRIVE_EN: U2.79 (P0[6]/I2SRX_SDA/SSEL1/MAT2[0]); also elsewhere on the board
DRIVE_ERR: U2.78 (P0[7]/I2STX_CLK/SCK1/MAT2[1]); also elsewhere on the board
EEPROM_SCL: R3.1, U1.6 (SCL), U2.24 (P0[28]/SCL0/USB_SCL)
EEPROM_SDA: R2.1, U1.5 (SDA), U2.25 (P0[27]/SDA0/USB_SDA)
ENCODER_A: U2.34 (P1[20]/MCI0/PWM1[2]/SCK0); also elsewhere on the board
ENCODER_B: U2.37 (P1[23]/MCI1/PWM1[4]/MISO0); also elsewhere on the board
ENCODER_Z: U2.38 (P1[24]/MCI2/PWM1[5]/MOSI0); also elsewhere on the board
ETH_CLK_EN: U2.43 (P1[27]/CLKOUT/*USB_OVRCR/CAP0[1])
ETH_CRS: U2.92 (P1[8]/ENET_CRS); also elsewhere on the board
ETH_MDC: U2.87 (P1[16]/ENET_MDC); also elsewhere on the board
ETH_MDIO: U2.86 (P1[17]/ENET_MDIO); also elsewhere on the board
ETH_RST: U2.44 (P1[28]/MCOA2/PCAP1[0]/MAT0[0]); also elsewhere on the board
ETH_RXD_0: U2.91 (P1[9]/ENET_RXD0); also elsewhere on the board
ETH_RXD_1: U2.90 (P1[10]/ENET_RXD1); also elsewhere on the board
ETH_RX_ER: U2.89 (P1[14]/ENET_RX_ER); also elsewhere on the board
ETH_TXD_0: U2.95 (P1[0]/ENET_TXD0); also elsewhere on the board
ETH_TXD_1: U2.94 (P1[1]/ENET_TXD1); also elsewhere on the board
ETH_TXD_EN: U2.93 (P1[4]/ENET_TX_EN); also elsewhere on the board
ETH_X1: U2.88 (P1[15]/ENET_REF_CLK); also elsewhere on the board
FAN_1_PWM: U2.75 (P2[0]/PWM1[1]/TXD1); also elsewhere on the board
FAN_1_SENSOR: U2.77 (P0[8]/I2STX_WS/MISO1/MAT2[2]); also elsewhere on the board
FAN_2_PWM: U2.74 (P2[1]/PWM1[2]/RXD1); also elsewhere on the board
FAN_2_SENSOR: U2.76 (P0[9]/I2STX_SDA/MOSI1/MAT2[3]); also elsewhere on the board
GND: C1.-, C2.2, C3.2, C4.2, C5.2, C6.2, C7.2, C8.2, C9.2, C10.2, C11.2, C12.2, JP1.2, R10.2, SW1.1 (2), SW1.2, SW2.1 (2), SW2.2, U1.1 (A0), U1.2 (A1), U1.3 (A2), U1.4 (GND), U2.11 (VSSA), U2.15 (VREFN), U2.31 (VSS_2), U2.41 (VSS_3), U2.55 (VSS_4), U2.72 (VSS_5), U2.83 (VSS_6), U2.97 (VSS), X2.2 (GND), X3.- (VBAT-); also elsewhere on the board
HMI_BUTTON_CPU_1: U2.63 (P0[16]/RXD1/SSEL0/SSEL); also elsewhere on the board
HMI_BUTTON_CPU_2: U2.62 (P0[15]/TXD1/SCK0/SCK); also elsewhere on the board
HMI_BUTTON_CPU_3: U2.61 (P0[17]/CTS1/MISO0/MISO); also elsewhere on the board
HMI_BUTTON_CPU_4: U2.60 (P0[18]/DCD1/MOSI0/MOSI); also elsewhere on the board
HMI_BUTTON_CPU_5: U2.59 (P0[19]/DSR1/SDA1); also elsewhere on the board
HMI_BUTTON_CPU_6: R4.2, R5.1; also elsewhere on the board
HMI_BUTTON_MCU_FCT_6: R5.2, U2.58 (P0[20]/DTR1/SCL1)
HMI_LCD_BACKLIGHT: U2.56 (P0[22]/RTS1/TD1); also elsewhere on the board
HMI_LCD_SCL: U2.49 (P0[11]/RXD2/SCL2/MAT3[1]); also elsewhere on the board
HMI_LCD_SDA: U2.48 (P0[10]/TXD2/SDA2/MAT3[0]); also elsewhere on the board
HMI_LED_1: U2.73 (P2[2]/PWM1[3]/CTS1/TRACEDATA[3]); also elsewhere on the board
HMI_LED_2: U2.70 (P2[3]/PWM1[4]/DCD1/TRACEDATA[2]); also elsewhere on the board
HMI_LED_3: U2.69 (P2[4]/PWM1[5]/DSR1/TRACEDATA[1]); also elsewhere on the board
HMI_LED_4: U2.68 (P2[5]/PWM1[6]/DTR1/TRACEDATA[0]); also elsewhere on the board
ISP_RXDO: U2.99 (P0[3]/RXD0/AD0[6]); also elsewhere on the board
ISP_TXDO: U2.98 (P0[2]/TXD0/AD0[7]); also elsewhere on the board
JTAG_TCK: U2.5 (TCK/SWDCLK); also elsewhere on the board
JTAG_TDI: U2.2 (TDI); also elsewhere on the board
JTAG_TDO: U2.1 (TDO/SWO); also elsewhere on the board
JTAG_TMS: U2.3 (TMS/SWDIO); also elsewhere on the board
LED_DEBUG: LED1.A, U2.35 (P1[21]/*MCABORT/PWM1[3]/SSEL0)
unnamed: R7.1, R8.2, R9.2, SW2.3 (1), SW2.4 (1)
unnamed: JP1.1, R1.1, U1.7 (WP)
unnamed: LED1.C, R10.1
RESET: R4.1, R6.1, SW1.3 (1), SW1.4 (1); also elsewhere on the board
RTCX1: C5.1, U2.16 (RTCX1), X1.1
RTCX2: C10.1, U2.18 (RTCX2), X1.2
USB_D_N: U2.30 (P0[30]/USB_D?); also elsewhere on the board
USB_D_P: U2.29 (P0[29]/USB_D+); also elsewhere on the board
USB_UP_LED: U2.32 (P1[18]/USB_UP_LED/PWM1[1]/CAP1[0]); also elsewhere on the board
USB_V_BUS: U2.21 (P1[30]/VBUS/AD0[4]); also elsewhere on the board
VBAT+: U2.19 (VBAT), X3.+1 (VBAT+), X3.+2 (VBAT+)
XTAL1: U2.22 (XTAL1), X2.3 (OUT)


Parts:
C13, C14, C15, C16, C17, C18, C19, C20, C21: 0.1uF; C0603; MPN MC0603B104K160CT
H1, H2, H3, H4: MOUNT-HOLE3.0; 3,0
J1, J2, J10: 22-05-7068-06; 7395-06; MPN 22-05-7068
J3, J9: 22-05-7028-02; 7395-02; MPN 22-05-7028
J4, J5, J7: 22-05-7038-03; 7395-03; MPN 22-05-7038
J6, J8, J11, J14: 22-05-7048-04; 7395-04; MPN 22-05-7048
J12: 22-27-2061-06; 6410-06; MPN 22-27-2061
J13: USB3075-30-A; USB_MICROB_SMT; MPN USB3075-30-A
J15: 1241050-5; 2.54/2X5; MPN 1241050-5
LED2: Blue; CHIPLED_0603; MPN OVS-0603
R11, R12, R13, R14, R15, R16, R17, R18, R19, R20, R21, R22, R23, R24, R28, R39, R40, R41, R42: 100; R0603; MPN MCMR06X1000FTL
R25, R27: 4K7; R0603; MPN MCMR06X4701FTL
R26, R30, R31: 33; R0603; MPN MCMR06X33R0FTL
R29, R32: 1K5; R0603; MPN MCMR06X1501FTL
R33, R34, R35, R36, R37, R38: 1K; R0603; MPN MCMR06X1001FTL
T1: MMBT2222AL; SOT−23; MPN MMBT2222ALT1G
U3: TPL0401A; SC-70-DCK; MPN ISL90728WIE627Z-TK
U4, U5: SN74LVC3G17DCTR; SOP65P400X130-8N

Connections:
+3V3: C20.1, C21.1, J4.2, J15.1, LED2.A, R25.1, R27.1, R32.1, U4.8 (VCC), U5.8 (VCC); also elsewhere on the board
+5V: C13.1, J9.1, R26.1, U3.1 (VDD), U3.6 (H)
ADC_SLACK_DETECTION: R13.2; also elsewhere on the board
ADC_TEMP_0: R11.2; also elsewhere on the board
ADC_TEMP_1: R12.2; also elsewhere on the board
AVDD: J4.1; also elsewhere on the board
BRAKE_SENSOR_1: R17.2; also elsewhere on the board
BRAKE_SENSOR_2: R14.2; also elsewhere on the board
CAN_RX: J3.1; also elsewhere on the board
CAN_TX: J3.2; also elsewhere on the board
DRIVE_EN: R15.2; also elsewhere on the board
DRIVE_ERR: R16.2; also elsewhere on the board
ENCODER_A: R18.2; also elsewhere on the board
ENCODER_B: R19.2; also elsewhere on the board
ENCODER_Z: R20.2; also elsewhere on the board
ETH_CRS: J1.3; also elsewhere on the board
ETH_MDC: J1.4; also elsewhere on the board
ETH_MDIO: J1.5; also elsewhere on the board
ETH_RST: J1.6; also elsewhere on the board
ETH_RXD_0: J2.5; also elsewhere on the board
ETH_RXD_1: J2.4; also elsewhere on the board
ETH_RX_ER: J2.6; also elsewhere on the board
ETH_TXD_0: J2.2; also elsewhere on the board
ETH_TXD_1: J2.1; also elsewhere on the board
ETH_TXD_EN: J2.3; also elsewhere on the board
ETH_X1: J1.1; also elsewhere on the board
FAN_1_PWM: R21.2; also elsewhere on the board
FAN_1_SENSOR: R22.2; also elsewhere on the board
FAN_2_PWM: R23.2; also elsewhere on the board
FAN_2_SENSOR: R24.2; also elsewhere on the board
GND: C13.2, C14.2, C15.2, C16.2, C17.2, C18.2, C19.2, C20.2, C21.2, J1.2, J4.3, J9.2, J12.1, J13.5, J15.2, T1.2 (E), U3.2 (GND), U4.4 (GND), U5.4 (GND); also elsewhere on the board
HMI_BUTTON_1: J10.1, R33.1
HMI_BUTTON_2: J10.2, R34.1
HMI_BUTTON_3: J10.3, R35.1
HMI_BUTTON_4: J10.4, R36.1
HMI_BUTTON_5: J10.5, R37.1
HMI_BUTTON_6: J10.6, R38.1
HMI_BUTTON_CPU_1: U4.1 (1A); also elsewhere on the board
HMI_BUTTON_CPU_2: U4.3 (2A); also elsewhere on the board
HMI_BUTTON_CPU_3: U4.6 (3A); also elsewhere on the board
HMI_BUTTON_CPU_4: U5.1 (1A); also elsewhere on the board
HMI_BUTTON_CPU_5: U5.3 (2A); also elsewhere on the board
HMI_BUTTON_CPU_6: U5.6 (3A); also elsewhere on the board
HMI_LCD_BACKLIGHT: R28.2; also elsewhere on the board
HMI_LCD_LED+: J11.1, R26.2, T1.3 (C)
HMI_LCD_SCL: J11.2, R25.2, U3.3 (SCL); also elsewhere on the board
HMI_LCD_SDA: J11.3, R27.2, U3.4 (SDA); also elsewhere on the board
HMI_LCD_VO: J11.4, U3.5 (W)
HMI_LED_1: R39.1; also elsewhere on the board
HMI_LED_2: R40.2; also elsewhere on the board
HMI_LED_3: R41.1; also elsewhere on the board
HMI_LED_4: R42.2; also elsewhere on the board
ISP_RXDO: J12.4, J15.3; also elsewhere on the board
ISP_TXDO: J12.5, J15.4; also elsewhere on the board
JTAG_TCK: J15.8; also elsewhere on the board
JTAG_TDI: J15.7; also elsewhere on the board
JTAG_TDO: J15.9; also elsewhere on the board
JTAG_TMS: J15.10; also elsewhere on the board
unnamed: J14.2, R40.1
unnamed: J14.4, R42.1
unnamed: J7.1, R18.1
unnamed: J7.2, R19.1
unnamed: J7.3, R20.1
unnamed: R28.1, T1.1 (B)
unnamed: J8.1, R21.1
unnamed: J8.2, R22.1
unnamed: J8.3, R23.1
unnamed: J8.4, R24.1
unnamed: J5.3, R13.1
unnamed: J5.2, R12.1
unnamed: J5.1, R11.1
unnamed: J13.2, R30.1, R32.2
unnamed: J13.3, R31.1
unnamed: C14.1, R33.2, U4.7 (1Y)
unnamed: LED2.C, R29.1
unnamed: C16.1, R34.2, U4.5 (2Y)
unnamed: C18.1, R35.2, U4.2 (3Y)
unnamed: J6.4, R16.1
unnamed: J6.3, R15.1
unnamed: J6.2, R14.1
unnamed: C15.1, R36.2, U5.7 (1Y)
unnamed: C17.1, R37.2, U5.5 (2Y)
unnamed: C19.1, R38.2, U5.2 (3Y)
unnamed: J6.1, R17.1
unnamed: J14.1, R39.2
unnamed: J14.3, R41.2
RESET: J15.5; also elsewhere on the board
USB_D_N: R31.2; also elsewhere on the board
USB_D_P: R30.2; also elsewhere on the board
USB_UP_LED: R29.2; also elsewhere on the board
USB_V_BUS: J13.1; also elsewhere on the board

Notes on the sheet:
USB
JTAG



Board: 4 copper layers, 90.6 x 41.0 mm, 102 parts (30 on the bottom side), 104 nets.

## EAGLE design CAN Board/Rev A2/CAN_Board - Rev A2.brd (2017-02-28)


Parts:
C1: 4700pF; C0603; MPN MC0603B472K500CT
C2: 100nF; C0603; MPN MC0603B104K250CT
H1, H2, H3, H4: MOUNT-HOLE3.0; 3,0
J1, J3: 22-05-7028-02; 7395-02; MPN 22-05-7028
J2: 5504F1-09S-02A-03; 5504F1-09S-02A; MPN 5504F1-09S-02A-03
JP1, JP2, JP3, JP4: FIDUCIAL1X2; FIDUCIAL-1X2
R1, R2: 60.4; R0603; MPN MCMR06X60R4FTL
T1: EXMACHINA-LOGO-NAME; EXM-LOGO-BASELINE
U1: MCP2561-E/SN; SOIC127P600X175-8N; MPN MCP2561-E/SN
X1: MSTBA2

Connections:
+5V: C2.1, J1.1, U1.3 (VDD)
+24V: J2.9, X1.1
CAN_N: J2.2, R1.1, U1.6 (CANL)
CAN_P: J2.7, R2.2, U1.7 (CANH)
CAN_RX: J3.1, U1.4 (RXD)
CAN_SHLD: J2.5
CAN_SPLIT: C1.2, U1.5 (SPLIT)
CAN_TX: J3.2, U1.1 (TXD)
GND: C2.2, J1.2, J2.3, J2.6, U1.2 (VSS), U1.8 (STBY), X1.2
unnamed: C1.1, R1.2, R2.1


Board: 2 copper layers, 57.0 x 41.0 mm, 18 parts (1 on the bottom side), 9 nets.

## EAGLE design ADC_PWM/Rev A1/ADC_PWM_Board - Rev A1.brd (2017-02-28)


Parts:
C1, C2, C3, C4, C5, C6, C7, C8, C9, C10: 0.1uF; C0603; MPN MC0603B104K250CT
CC1: CC-BY-NC-SA
H1, H2, H3, H4: MOUNT-HOLE3.0; 3,0
J1, J2, J9: 22-05-7028-02; 7395-02; MPN 22-05-7028
J3, J4, J5, J8: 22-05-7048-04; 7395-04; MPN 22-05-7048
J6, J11, J12: 22-05-7038-03; 7395-03; MPN 22-05-7038
J7: 22-05-7058-05; 7395-05; MPN 22-05-7058
J10: MSTBA2
JP1, JP2, JP3, JP4: FIDUCIAL1X2; FIDUCIAL-1X2
R1, R2: 10K; R0603; MPN MCMR06X1002FTL
R3, R6: 1K8; R0603; MPN MCMR06X1801FTL
R4, R5, R8, R9, R11, R12: 1K; R0603; MPN MCMR06X1001FTL
R7, R10: 1K2; R0603; MPN MCMR06X1201FTL
R13, R14, R18, R19, R20: 100; R0603; MPN MCMR06X1000FTL
R15, R16, R17: 2K7; R0603; MPN MCMR06X4701FTL
T1: EXMACHINA-LOGO-NAME; EXM-LOGO-BASELINE
U1: TLV313; SOT23-DBV; MPN TLV313IDBVT
U2: HCPL0631; SOIC08; MPN HCPL-0631-500E
U3: SN74LVC3G17DCTR; SOP65P400X130-8N

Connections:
+3V3: C3.1, C6.1, C10.1, J11.2, R11.2, R12.2, U1.5 (V+), U2.8 (VCC), U3.8 (VCC)
+5V: J3.1, J7.4, J9.1, R15.1, R16.1, R17.1
+24V: J4.1, J5.1, J10.1
ADC_SLACK_DETECTION: J6.3, R10.1, U1.1 (OUT)
ADC_TEMP_0: C1.1, J6.1, R4.1
ADC_TEMP_1: C2.1, J6.2, R5.2
AVDD: J1.1, J2.1, J11.1
ENCODER_A: J12.1, U3.7 (1Y)
ENCODER_B: J12.2, U3.5 (2Y)
ENCODER_Z: J12.3, U3.2 (3Y)
FAN_1_PWM: J8.1, R8.2
FAN_1_SENSOR: J8.2, U2.7 (VO)
FAN_2_PWM: J8.3, R9.2
FAN_2_SENSOR: J8.4, U2.6 (VO2)
GND: C1.2, C2.2, C3.2, C4.2, C5.2, C6.2, C7.2, C8.2, C9.2, C10.2, J3.4, J4.4, J5.4, J7.1, J9.2, J10.2, J11.3, R1.1, R2.2, R7.1, U1.2 (V-), U2.2 (C1), U2.3 (C2), U2.5 (GND), U3.4 (GND)
unnamed: J4.3, R11.1, R13.1
unnamed: J5.3, R12.1, R14.1
unnamed: C4.1, R13.2, U2.1 (A1)
unnamed: C5.1, R14.2, U2.4 (A2)
unnamed: J4.2, R8.1
unnamed: J5.2, R9.1
unnamed: J3.2, R3.1
unnamed: J7.3, R15.2, R18.1
unnamed: J7.5, R16.2, R19.1
unnamed: J7.2, R17.2, R20.1
unnamed: C9.1, R20.2, U3.6 (3A)
unnamed: C8.1, R19.2, U3.3 (2A)
unnamed: C7.1, R18.2, U3.1 (1A)
unnamed: R3.2, R10.2, U1.3 (+IN)
unnamed: J1.2, R1.2, R4.2
unnamed: J2.2, R2.1, R5.1
unnamed: R6.2, R7.2, U1.4 (-IN)
unnamed: J3.3, R6.1

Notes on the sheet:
TEMPERATURE SENSOR
FAN
SLACK DETECTION



Board: 2 copper layers, 57.0 x 41.0 mm, 55 parts (3 on the bottom side), 33 nets.

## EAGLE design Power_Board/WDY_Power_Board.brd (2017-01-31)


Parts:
C1, C2, C5, C6: 2.2uF; C0603; MPN GRT188R61H225KE13D
C3, C4: 1000pF; C0603; MPN MC0603B102K500CT
C7, C8: 22uF; C0805; MPN MCMT21N220F250CT
D1: STPS3L40UF; SMB
D2, D3: MBRS140; DO-214AA; MPN MBRS140T3G
F1: FUSE3557L; 3557-LITTLE; MPN 3557
H1, H2, H3, H4: MOUNT-HOLE3.0; 3,0
J1, J2: 22-05-7028-02; 7395-02; MPN 22-05-7028
JP1, JP2, JP3, JP4: FIDUCIAL1X2; FIDUCIAL-1X2
L1: 10uH; WE-PD2_5848/5820; MPN 74477410
L2: 15uH; WE-PD2_5848/5820; MPN 744774115
LED1, LED2: Blue; CHIPLED_0603; MPN OVS-0603
LED3, LED4: Blue; CHIP-LED0603; MPN OVS-0604
R1, R2, R7: 31k6; R0603; MPN MC0063W060311K5
R3, R4: 4k7; R0603; MPN MCMR06X4701FTL
R5: 52k3; R0603; MPN MC0063W0603152K3
R6, R8: 10k; R0603; MPN MCMR06X1002FTL
R9, R10, R11, R12: 1k5; R0603; MPN MC0063W060311K5
TP1, TP2, TP3, TP5: TPB1,27; B1,27
U1, U2: LT3686HDDPBF; DFN300X300X80-11N
U$1: EXMACHINA-LOGO-NAME; EXM-LOGO-BASELINE
X1: MSTBA2

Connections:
+3V3: C7.1, J2.1, L1.2, R7.2, R10.2, R12.2, TP5.TP, U2.2 (BD)
+5V: C8.1, J1.1, L2.2, R5.2, R9.2, R11.2, TP2.TP, U1.2 (BD)
+24V: C1.1, C2.1, D1.C, F1.3 (2), F1.4 (2), R3.2, R4.2, TP1.TP, U1.1 (VIN), U1.6 (EN/UVLO), U2.1 (VIN), U2.6 (EN/UVLO)
GND: C1.2, C2.2, C3.2, C4.2, C7.2, C8.2, D1.A, J1.2, J2.2, LED2.C, LED3.C, LED4.C, R1.1, R2.1, R6.1, R8.1, R11.1, R12.1, TP3.TP, U1.7 (MODE), U1.11 (EP), U2.7 (MODE), U2.11 (EP), X1.2
unnamed: R1.2, U1.5 (RT)
unnamed: R7.1, R8.2, U2.3 (FB)
unnamed: C3.1, U1.4 (SS)
unnamed: R2.2, U2.5 (RT)
unnamed: C4.1, U2.4 (SS)
unnamed: R5.1, R6.2, U1.3 (FB)
unnamed: C6.1, U2.8 (BOOST)
unnamed: C5.1, U1.8 (BOOST)
unnamed: C5.2, D2.C, L2.1, U1.10 (SW)
unnamed: D2.A, U1.9 (DA)
unnamed: C6.2, D3.C, L1.1, U2.10 (SW)
unnamed: D3.A, U2.9 (DA)
unnamed: LED2.A, R4.1
unnamed: LED1.C, R3.1
unnamed: LED4.A, R10.1
unnamed: LED3.A, R9.1
VIN: F1.1, F1.2 (1), LED1.A, X1.1


Board: 2 copper layers, 57.0 x 41.0 mm, 48 parts (0 on the bottom side), 21 nets.

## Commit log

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2017-01-06 Move project folders to root
    [Ethernet_Board.brd, Ethernet_Board.sch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]
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2017-01-06 Add TX and RX on bPlace layer
    [CAN_Board.brd]
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2017-01-09 Update components names and value placement
    [WDY_Power_Board.brd]
2017-01-10 Replace output connector and generate gerber files
    [CAN_Board.brd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]
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2017-01-11 Generate CAN Board BOM
    [CAN_Board_Rev_A1_BOM.xlsx]
2017-01-11 Generate Ethernet Board BOM
    [Ethernet_Board_Rev_A1_BOM.xlsx]
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2017-01-12 Add fabrication folder + clean folder
    [CAN_Board.brd, WDY_CAN_Board_Part_List.xlsx]
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2017-01-17 Route the MCU board
    [MCU_Board.brd, MCU_Board.sch]
2017-01-17 Add Relay proto border
    [Relay_Board.brd, Relay_Board.sch]
2017-01-17 Add fillet to the board
    [Relay_Board.brd]
2017-01-17 Add limitation resistance on Encoder output, ADC input, relay input and fan Add LED on board Poly for +5V on Route15
    [MCU_Board.brd, MCU_Board.sch]
2017-01-17 Add free-wheel diode on the schematic and re-route the board
    [Relay_Board.brd, Relay_Board.sch]
2017-01-18 Add fiducial to the board
    [Relay_Board.brd, Relay_Board.sch]
2017-01-18 Add rev A2 to the HMI board Change hole placement
    [HMI_Board.brd, HMI_Board.sch]
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2017-01-18 Change name and value size on the board
    [Relay_Board.brd, Relay_Board.sch]
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2017-01-20 Add pin name on the board
    [MCU_Board.brd, MCU_Board.sch]
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2017-01-20 Add documentation on the board
    [Relay_Board.brd]
2017-01-20 Add ADC + Fan + Encoder proto board
    [ADC_PWM_Board.brd, ADC_PWM_Board.sch]
2017-01-23 Add opto to the Fan sensor and finsh to route it
    [ADC_PWM_Board.brd, ADC_PWM_Board.sch]
2017-01-23 Add decoupling capacitor to the opto
    [ADC_PWM_Board.brd, ADC_PWM_Board.sch]
2017-01-24 Replacing name and value on the board
    [ADC_PWM_Board.brd, ADC_PWM_Board.sch]
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2017-01-24 Generate gerber files and BOM and part list
    [MCU_Board.brd, MCU_Board.csv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]
2017-01-25 Clean folder and generate the top and bottom placement
    [MCU_Board.csv]
2017-01-31 Add mechanical layer and update part list
    [ADC_PWM_Board.brd, WDY_ADC_PWM_Board_Part_List.xlsx]
2017-02-17 Add ABK electronic board
    [ABK-ECS - Rev A1.brd, ABK-ECS - Rev A1.sch]
2017-02-23 Route the board and modify schematic
    [ABK-ECS - Rev A1.brd, ABK-ECS - Rev A1.sch]
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2017-02-23 Rename guard ring to GND Put GND via under alim component Add a pull-down to WP on AT24
    [ABK-ECS - Rev A1.brd, ABK-ECS - Rev A1.sch]
2017-02-23 Add LEDs on input and output
    [ABK-ECS - Rev A1.brd, ABK-ECS - Rev A1.sch]
2017-02-23 Place Logo and add name on the board
    [ABK-ECS - Rev A1.brd]
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2017-02-24 Add solderJump to the usb shield and replace layer 3 into 15
    [ABK-ECS - Rev A1.brd, ABK-ECS - Rev A1.sch]
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2017-02-28 Add rev A1 folder, create folder rev A2 and modify the board
    [ADC_PWM_Board - Rev A1.brd, ADC_PWM_Board - Rev A1.sch, ADC_PWM_Board - Rev A2.brd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]
2017-02-28 Add rev A2 to the folder
    [CAN_Board - Rev A1.brd, CAN_Board - Rev A1.sch, CAN_Board - Rev A2.brd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]
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2017-03-13 Update Main Board Rev A1 project and add Rev A2
    [Main_Board_Rev_A2.brd, Main_Board_Rev_A2.sch]
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2017-03-15 Place component on the board
    [Main_Board_Rev_A2.brd, Main_Board_Rev_A2.sch]
2017-03-17 Route Ethernet on the main board
    [Main_Board_Rev_A2.brd, Main_Board_Rev_A2.sch]
2017-03-17 Update Relay proto board and regenerate top placement
    [Relay_Board.brd, Relay_Board.sch]
2017-03-17 Update part list of power proto board
    [WDY_Power_Board_Part_List.xlsx]
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2017-03-22 Route all the signals (except power net)
    [Main_Board_Rev_A2.brd, Main_Board_Rev_A2.sch]
2017-04-24 Add the sizing on the board
    [HMI_Board.brd]
2017-04-24 Route power and add guard ring on the board
    [Main_Board_Rev_A2.brd, Main_Board_Rev_A2.sch]
2017-04-26 Adjust the position of the component
    [HMI_Board.brd]
2017-05-02 Add description on the connector
    [Main_Board_Rev_A2.brd, Main_Board_Rev_A2.sch]
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2017-05-05 Name sheet 6 and add +5V output for ethernet switch
    [Main_Board_Rev_A2.brd, Main_Board_Rev_A2.sch]
2017-05-05 Put CAN on the top
    [Main_Board_Rev_A2.brd]
2017-05-05 Put ethernet connector on the top
    [Main_Board_Rev_A2.brd]
2017-05-05 Modified +24V poly near DB9 connector
    [Main_Board_Rev_A2.brd]
2017-05-05 Enlarge +24V nets and GND of the buck converter
    [Main_Board_Rev_A2.brd]
2017-05-05 Deleted orphan wire near the fuse holder
    [Main_Board_Rev_A2.brd]
2017-05-09 Renamed HMI_BUTTON_CPU nets to HMI_BUTTON_ISO
    [Main_Board_Rev_A2.brd, Main_Board_Rev_A2.sch]
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2017-05-09 Repalce the HMI_LCD_LED+ npn interface into pnp interface
    [Main_Board_Rev_A2.brd, Main_Board_Rev_A2.sch]
2017-05-09 63 to 10k and add two test pad on EEPROM protection
    [Main_Board_Rev_A2.brd, Main_Board_Rev_A2.sch]
2017-05-09 add Pull-up resistor on USB_D_N for speed configuration
    [Main_Board_Rev_A2.brd, Main_Board_Rev_A2.sch]
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2017-05-09 Replace mounting hole M2.5 to M3 and add guard ring on inner layer
    [Main_Board_Rev_A2.brd, Main_Board_Rev_A2.sch]
2017-05-18 Change load pin gain and change to pull-up HMI_LCD_LED+
    [Main_Board_Rev_A2.brd, Main_Board_Rev_A2.sch]
2017-05-22 nvert IO on U3 and U4 and transistor T1 on pull up output
    [Main_Board_Rev_A2.brd, Main_Board_Rev_A2.sch]
2017-05-22 Replace Drive error and enable connectors to 3pts molex
    [Main_Board_Rev_A2.brd, Main_Board_Rev_A2.sch]
2017-05-22 Replace load pin connector into 5pts molex connector with GND MECA
    [Main_Board_Rev_A2.brd, Main_Board_Rev_A2.sch]
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2017-06-06 Add MDP folder to HMI Board rev A2
    [HMI_Board.brd, HMI_Board.sch, HMI_Board_Rev_A1_BOM.xls]
2017-06-07 Correct panel and generate Gerber
    [HMI_Board.brd, HMI_Board_Rev_A1_BOM.xls]
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2017-06-08 Change Coil polarity on K1 and K2 Brake relay connect to NO Freewhell diode reverse Rename SIG into OUT Change trace of Brake Add 2pts connector for the reset
    [Safety_Board.kicad_pcb, Safety_Board.sch]
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2017-07-18 Invert relays footprint
    [Safety Board- Rev A2 - BOM.xlsx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]
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

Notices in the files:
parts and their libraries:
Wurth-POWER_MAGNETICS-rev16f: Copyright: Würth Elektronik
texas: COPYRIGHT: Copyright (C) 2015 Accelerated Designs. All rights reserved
